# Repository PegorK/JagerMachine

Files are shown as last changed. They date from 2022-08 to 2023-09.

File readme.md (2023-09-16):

# JÄGERMACHINE
<div align="center">
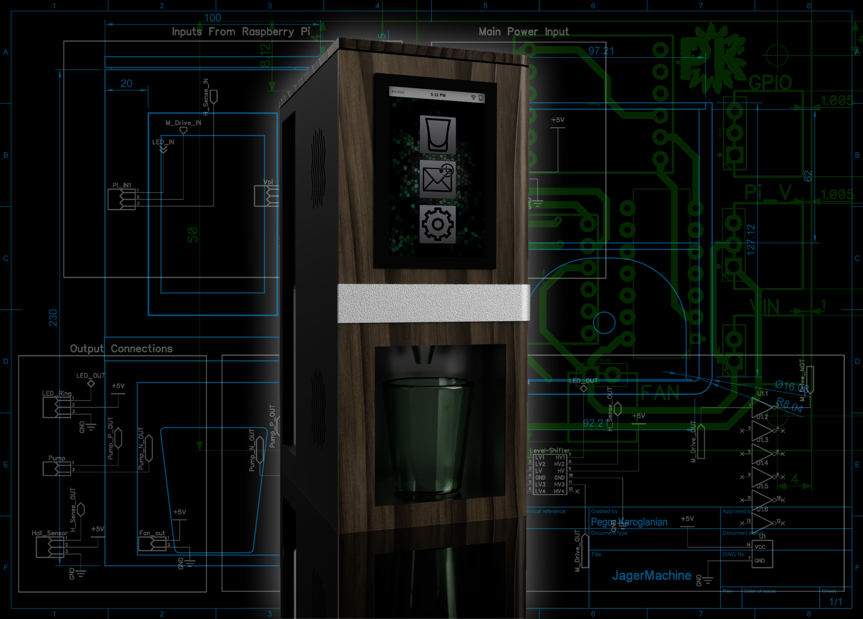
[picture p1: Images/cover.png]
CoverRender
  
</div>

The JägerMachine is an IoT shot pouring machine powered by a Raspberry Pi 3B+. It features a full GUI that allows the user to configure the device, pour a shot, and also check previous messages sent to the machine. Once paired with it's own GMail account, the JägerMachine waits for emails containing a secret user defined subject line and a custom message that gets displayed on the screen. Once an email is received a shot is poured :) 

Initially this project started as a gift for a friend. We always give each other Jagermeister related gifts as an inside joke, so I figured this would be PERFECT. It started out as a pretty bland render I threw together on Fusion 360 as seen below and slowly started getting more and more complicated.

<div align="center">
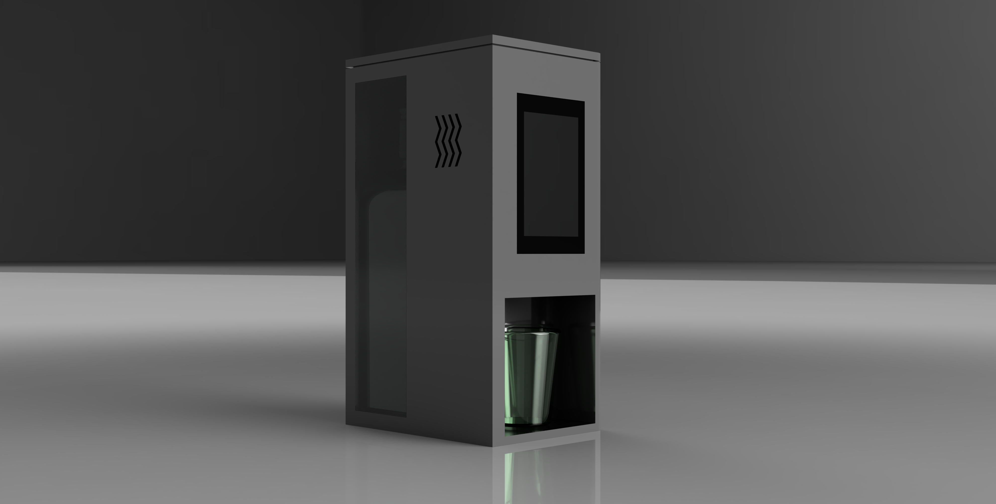
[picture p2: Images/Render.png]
First Render
  
  <br><b>Figure 1</b>: First render of the initial design.
</div>

Unfortunately I didn't finish the project in time for my friends birthday (sorry Jon :( ), but I continued on and kept adding features and I think It's finally done! Some of the features currently supported are as mentioned above are:
* Search for available WiFi connections and connect to them (see Figure 2 & 3).
* Manually pour a shot.
* Pour a shot via email with a a message that gets displayed.
* Hall effect sensor to detect when shot glass is placed/removed.
* Enable/Disable LEDs

<div align="center">
    <table>
        <tr>
            <td>
                <div align="center">
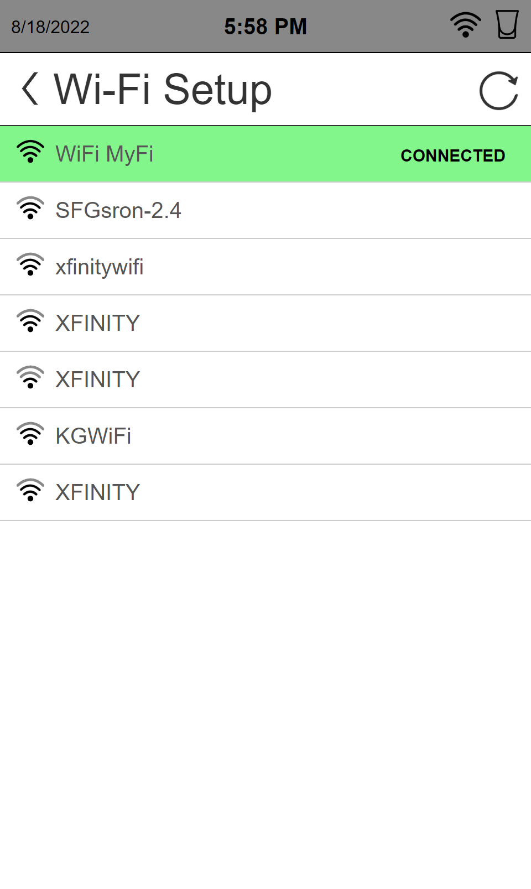
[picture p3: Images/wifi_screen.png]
Wifi Search Screen
                    
                    <br><b>Figure 2.</b>: Available WiFi connections list.
                </div>
            </td>
            <td>
                <div align="center">
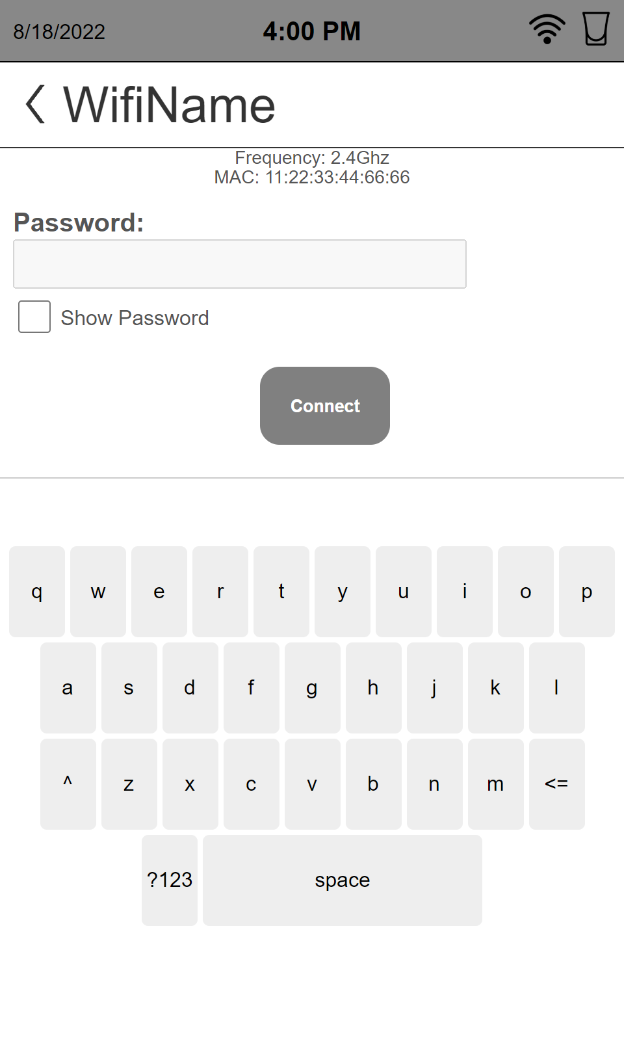
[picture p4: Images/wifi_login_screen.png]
Connect to Wifi
                    
                    <br><b>Figure 3</b>: Signing in to a WiFi connection.
                </div>
            </td>
        </tr>
    </table>
</div>
The hardware for this build wasn't too complicated. I used a logic level shifter to drive the WS2812B LED Ring since it requires 5V logic and RPi outputs 3.3V logic and an H-Bridge Motor driver module for the pump. The only funky part was that I had to use a Hex-Invert IC since the pins I decided to use on the Raspberry Pi are normally high until they are configured as outputs. 

To avoid having a ton of wires everywhere I designed a motherboard PCB that the breakout boards can easily pop onto. The files & schematic for this PCB are in the `Hardware` folder of this repo. The completed board can be seen below. 

<div align="center">
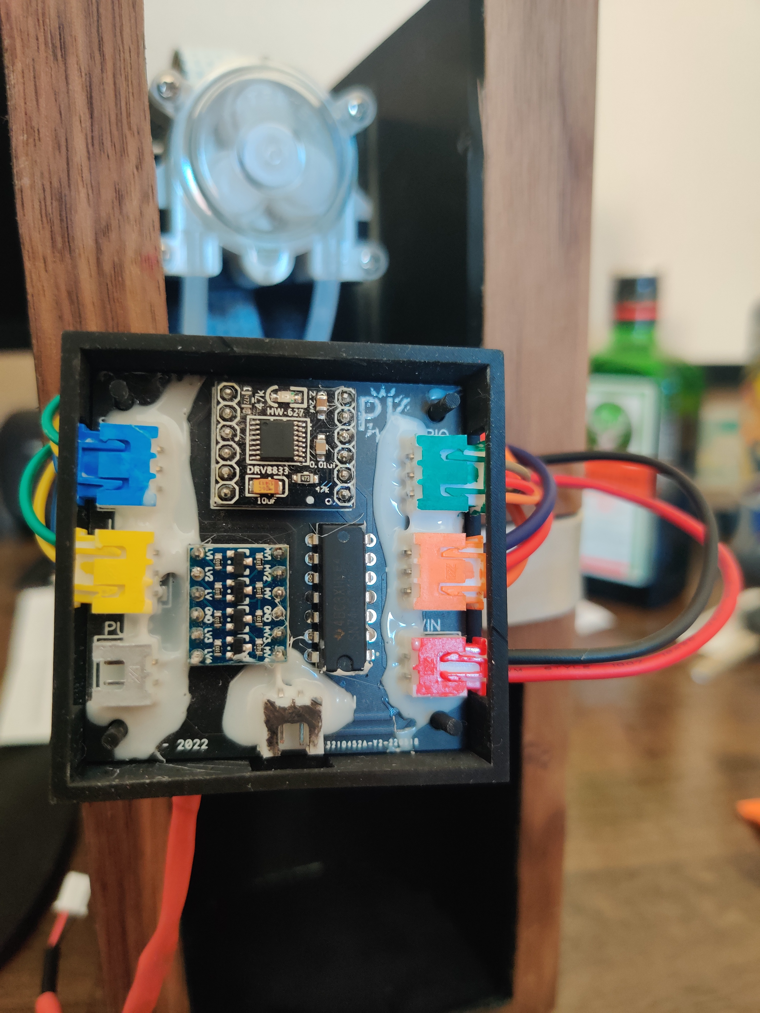
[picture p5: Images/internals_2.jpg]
PCB
    
    <br><b>Figure 4</b>: PCB to connect all peripherals.
</div>

Overall I'd say I got pretty close to the render and vision I originally had in mind. Below are a couple pictures of the JägerMachine booting and pouring a shot.

<div align="center">
    Booting
    <br><b>Figure 5.</b>: JägerMachine booting.
</div>

<div align="center">
    Pouring a shot
    <br><b>Figure 6.</b>: JägerMachine pouring a shot.
</div>

<div align="center">
    Side view
    <br><b>Figure 7.</b>: JägerMachine idle.
</div>

<b>More detailed info on the Raspberry Pi setup can be found below and more pictures are available in the `Images` folder.<b>

<br>

The build parts consist of:
* [3.5" DSI Touch Screen](https://www.amazon.com/dp/B08634Y16L?psc=1&ref=ppx_yo2ov_dt_b_product_details)
* [Peristaltic Pump](https://www.amazon.com/gp/product/B00HLCOXFI/ref=ppx_yo_dt_b_asin_title_o08_s00?ie=UTF8&psc=1)
* [WS2812B LED Ring](https://www.amazon.com/gp/product/B09B3K2XZL/ref=ppx_yo_dt_b_asin_title_o07_s00?ie=UTF8&psc=1)
* [Hall Effect Sensor](https://www.amazon.com/gp/product/B096S7Y2KH/ref=ppx_yo_dt_b_asin_title_o05_s00?ie=UTF8&psc=1)
* [Motor Drive Module (for pump)](https://www.amazon.com/gp/product/B08RMWTDLM/ref=ppx_yo_dt_b_asin_title_o06_s01?ie=UTF8&psc=1)
* [3.3V to 5V Level Shift (for LED ring)](https://www.amazon.com/HiLetgo-Channels-Converter-Bi-Directional-3-3V-5V/dp/B07F7W91LC)
* USB Storage (used to store WiFi info)
* (Optional) Custom PCB (Designed in DipTrace, ordered from PCBWay)
* (Optional) Custom 3D Printed Parts (enclosures, nozzle, pump holder, fan holder)(Designed in Fusion360 ordered from CraftCloud)

## Raspberry Pi Setup Instructions
1)	[Configure Rpi to Kiosk Mode](https://desertbot.io/blog/raspberry-pi-4-touchscreen-kiosk-setup-64-bit-bullseye)
1)	[Install NGINX Webserver (w/ PHP Installation)](https://pimylifeup.com/raspberry-pi-nginx/)
1)	[Enable Root SSH](https://howtovmlinux.com/articles/rasberry-pi/enable-root-login-and-change-password-raspberrypi/)
1)	[Disable BT (optional)](https://di-marco.net/blog/it/2020-04-18-tips-disabling_bluetooth_on_raspberry_pi/)
1)	[Rotate LCD (optional)](https://osoyoo.com/2019/09/20/instruction-for-raspberry-pi-5-dsi-touch-screen/)
1)	[Enable GPIOs](https://pimylifeup.com/raspberry-pi-gpio/)
1)	[Setup NeoPixel libraries](https://learn.adafruit.com/neopixels-on-raspberry-pi/python-usage)
1)	[Setup automount usb flash drive](https://www.shellhacks.com/raspberry-pi-mount-usb-drive-automatically/)
1)	[Add custom splash  (optional)](https://forums.raspberrypi.com/viewtopic.php?t=276545)
1)	[Remove warranty text and other text](https://blog.smittytone.net/2020/05/23/how-to-remove-a-pis-login-message/)
    1) [Hide all boot text](https://techoverflow.net/2021/10/19/how-to-hide-all-boot-text-blinking-cursor-on-raspberry-pi/)
    1) [Hide xorg messages](https://unix.stackexchange.com/questions/110805/debian-squeeze-hide-xorg-start-messages)
1)	[Give root privilege to custom script `runRoot.sh`](https://superuser.com/questions/1448987/allow-php-to-run-shell-script-with-sudo-permission)
1)  Copy over the folders in the `Software` folder (`custom_scripts`, `flags`, `html`, `services`) onto the Raspberry Pi, placing them in `/var/www/`
1)	`Chmod +x` all the scripts under `custom_scripts` folder.
1)	Link the services in the `services` folder to <b>systemd</b>
    1) `boot_complete.service`:
        ```
            systemctl enable /var/www/services/boot_complete.service
        ```
    1) `glass_check.service`:
        ```
            systemctl enable /var/www/services/glass_check.service
        ```
    1) `email_check.service`:
        ```
            systemctl enable /var/www/services/email_check.service
        ```
    1) `wifi_check.service`:
        ```
            systemctl enable /var/www/services/wifi_check.service
        ```
    1) `led_boot.service`:
        ```
            systemctl enable /var/www/services/led_boot.service
        ```
1) Edit the `emailConfig.py` file to your desired email configuration. You must use a GMail account that has two-factor authentication so you can use an app password. [More info on app passwords](https://support.google.com/accounts/answer/185833?hl=en)

### Contact
[Buy me a Coffee!](https://www.buymeacoffee.com/pegor)
<br>
devPegor@gmail.com

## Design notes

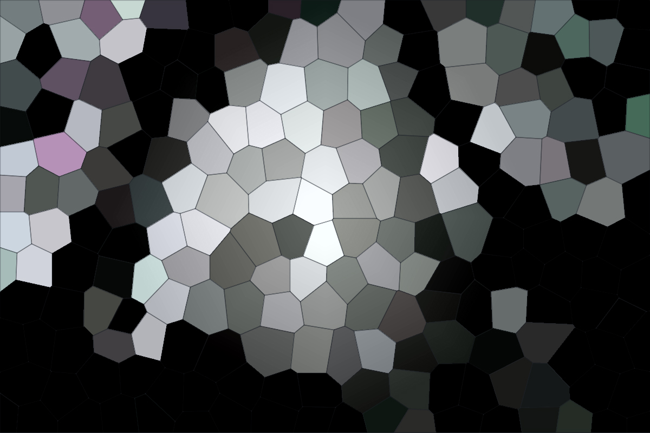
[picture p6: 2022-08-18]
Software/html/images/screen_saver/f_9.jpg

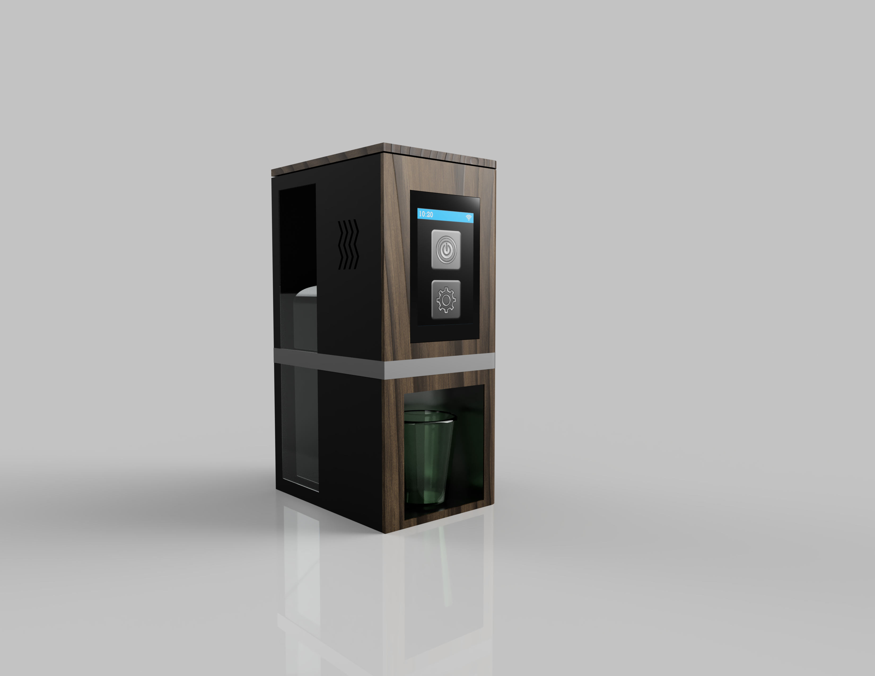
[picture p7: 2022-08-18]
Images/Render_2.png

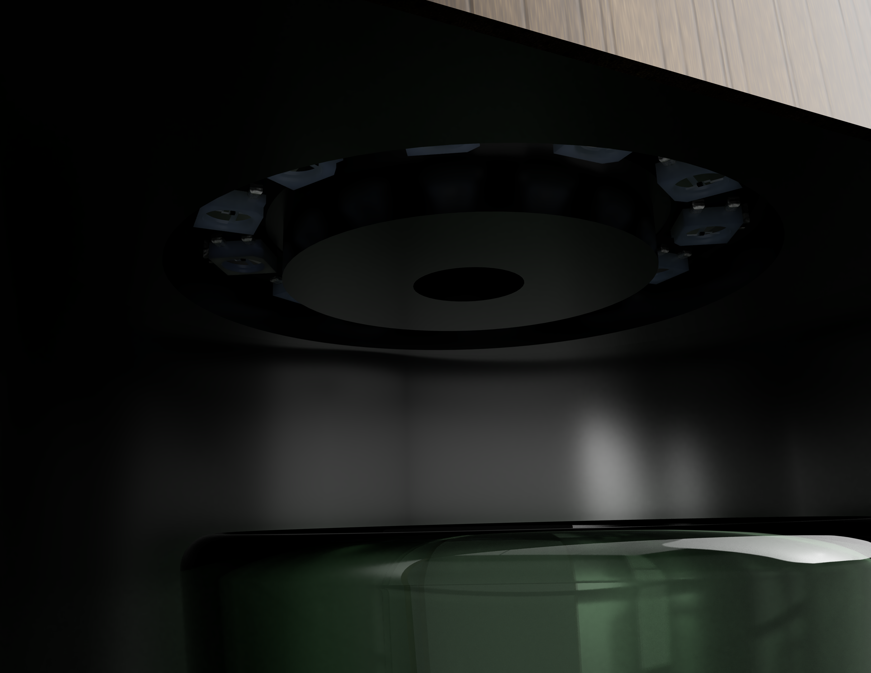
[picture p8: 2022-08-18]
Images/Render_6.png

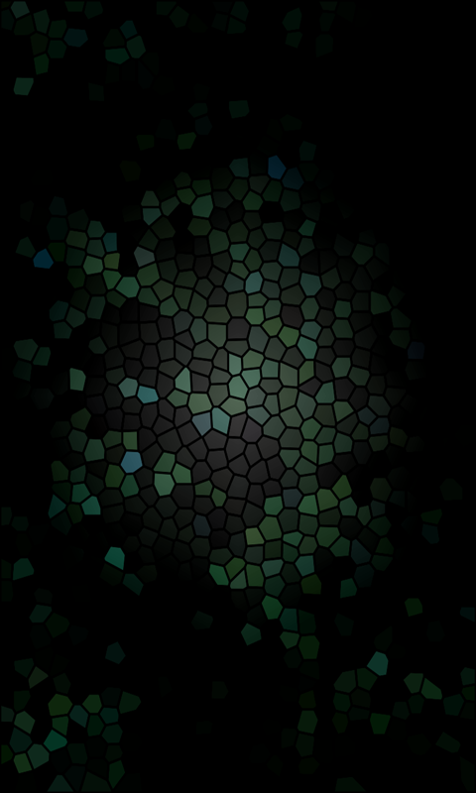
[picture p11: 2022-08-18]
Software/html/images/background_800x480.png

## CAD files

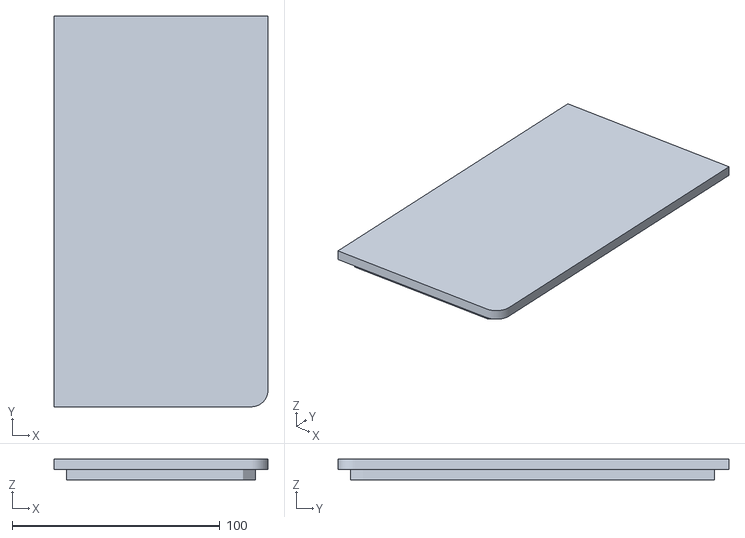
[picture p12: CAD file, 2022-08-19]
Hardware/3D Parts/Main_Lid.stl
103.0 x 188.0 x 10.0

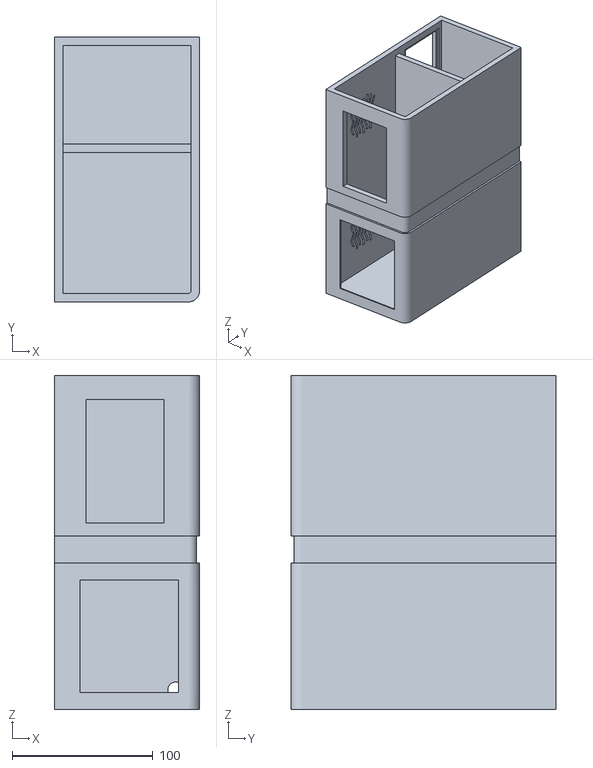
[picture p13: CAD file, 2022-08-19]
Hardware/3D Parts/Main.stl
103.0 x 188.0 x 237.0

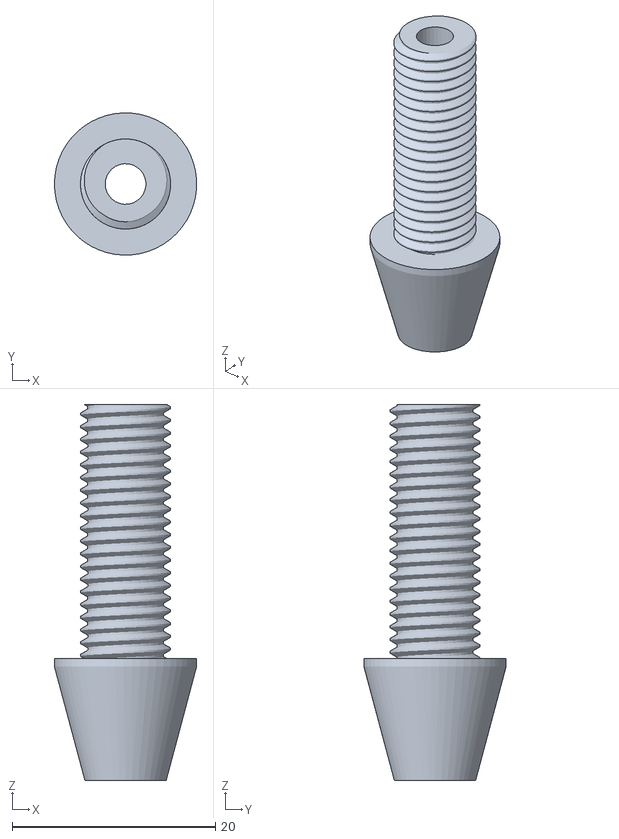
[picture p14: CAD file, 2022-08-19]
Hardware/3D Parts/Nozzle.stl
14.0 x 14.0 x 37.0

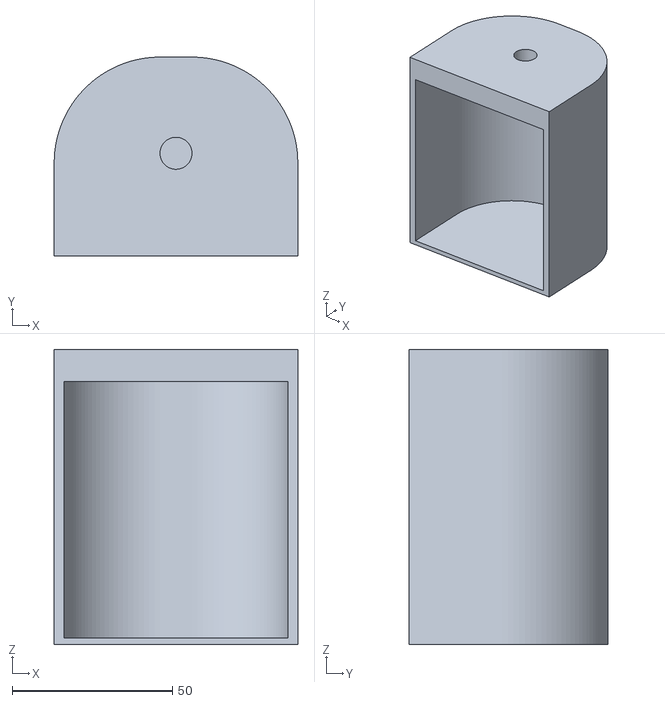
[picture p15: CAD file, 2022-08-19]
Hardware/3D Parts/Shot_Glass_Enclosure.stl
76.0 x 62.0 x 92.0

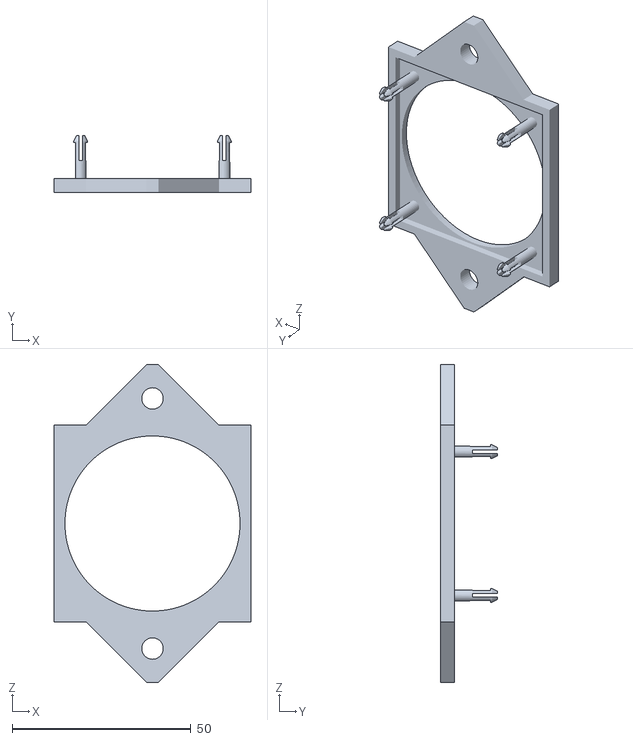
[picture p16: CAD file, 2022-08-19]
Hardware/3D Parts/Fan_Holder.stl
55.0 x 16.0 x 89.0

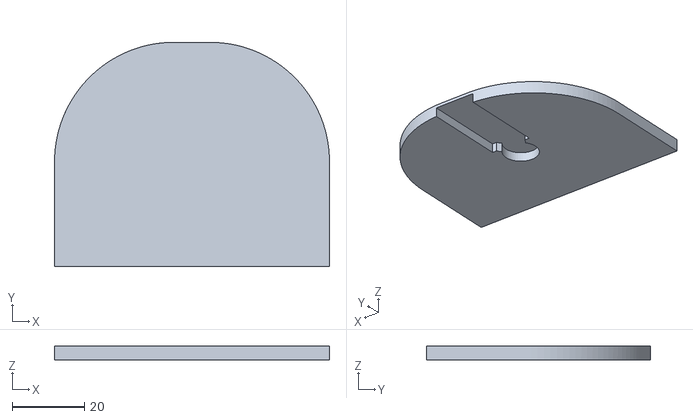
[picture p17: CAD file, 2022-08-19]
Hardware/3D Parts/Hall_Effect_Sensor_Board.stl
76.0 x 62.0 x 4.00

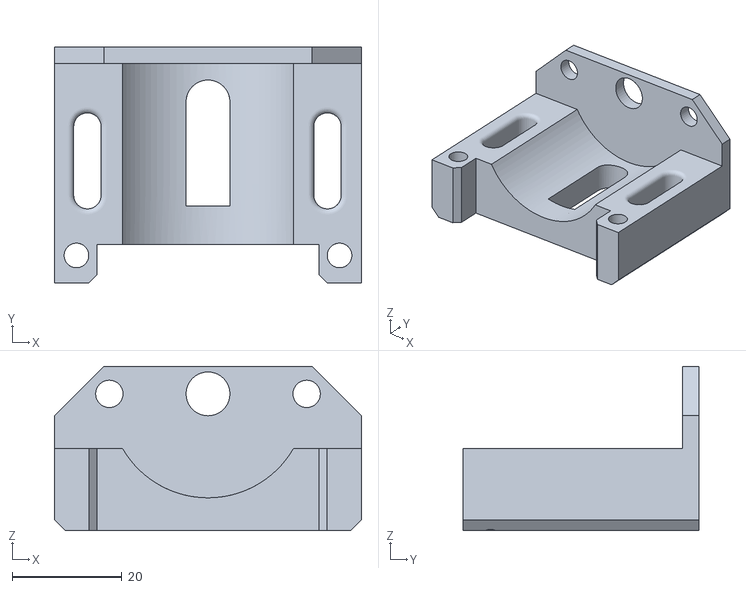
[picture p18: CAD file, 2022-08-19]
Hardware/3D Parts/Pump_Holder.stl
56.0 x 43.0 x 30.0

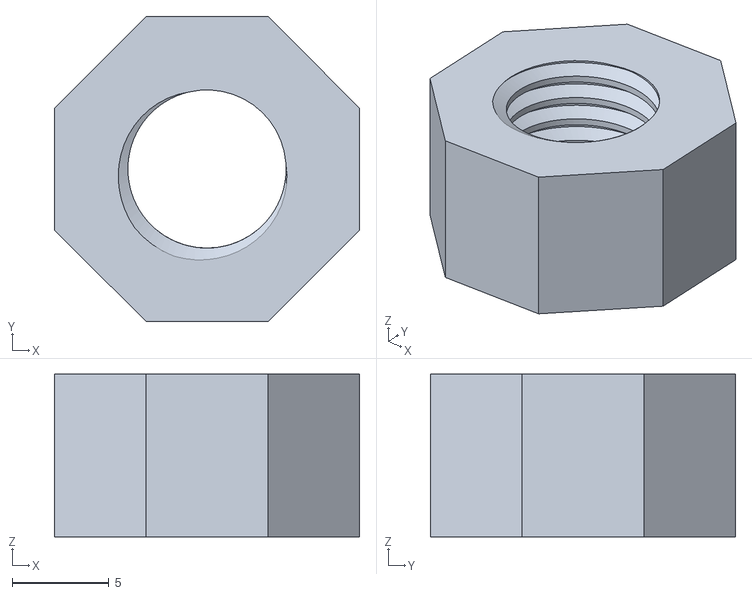
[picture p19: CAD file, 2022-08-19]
Hardware/3D Parts/Nozzle_Nut.stl
15.8 x 15.8 x 8.40

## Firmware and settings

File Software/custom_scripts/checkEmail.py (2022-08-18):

#!/usr/bin/env python

#==========================================
# Title:  checkEmail.py
# Author: Pegor Karoglanian + https://bc-robotics.com/tutorials/sending-email-using-python-raspberry-pi/ (For Emailer class)
# Date:   7/1/22
# Notes:  This script runs continuously and is started by the email-check.service on boot.
#==========================================

import smtplib
import imaplib
import email
import time
import os

import emailConfig as CONFIG

from datetime import datetime, timezone
from urllib.request import urlopen
from pathlib import Path

#Email Variables
SMTP_SERVER         = 'smtp.gmail.com' #Email Server (don't change!)
SMTP_PORT           = 587 #Server Port (don't change!)

GMAIL_USERNAME      = CONFIG.GMAIL_USERNAME
GMAIL_PASSWORD      = CONFIG.GMAIL_PASSWORD
ALLOWED_ADDRESS     = CONFIG.ALLOWED_ADDRESS
SECRET_PHRASE       = CONFIG.SECRET_PHRASE

TIME_THRESHOLD      = 10
RESPONSE_SUBJECT    = "GOT YOUR REQUEST"
RESPONSE_POUR       = "Pouring a shot now :)"
RESPONSE_WAIT       = "Looks like a shot has already been poured and waiting to be cleared. Try again later!"
RESPONSE_NOCUP      = "Look like the shot glass is not in place :( .Try again later!"
RESPONSE_UNK        = "UNKNOWN ERROR >:("

class Emailer:
    def checkNetwork(self):
        try:
            sysWifi = os.popen('sudo /var/www/custom_scripts/runRoot.sh checkOnline')
            return (sysWifi.read().split('\n')[0] == 'True')
        except: 
            return False

    def sendResponse(self, resp):
        #Create Headers
        headers = ["From: " + GMAIL_USERNAME, "Subject: " + RESPONSE_SUBJECT, "To: " + ALLOWED_ADDRESS,
        "MIME-Version: 1.0", "Content-Type: text/html"]
        headers = "\r\n".join(headers)

        #Connect to Gmail Server
        sendSession = smtplib.SMTP(SMTP_SERVER, SMTP_PORT)
        sendSession.ehlo()
        sendSession.starttls()
        sendSession.ehlo()

        #Login to Gmail
        sendSession.login(GMAIL_USERNAME, GMAIL_PASSWORD)

        #Send Email & Exit
        sendSession.sendmail(GMAIL_USERNAME, ALLOWED_ADDRESS, headers + "\r\n\r\n" + resp)
        sendSession.quit

    def checkMail(self):
        readSession = imaplib.IMAP4_SSL('imap.gmail.com')
        readSession.login(GMAIL_USERNAME, GMAIL_PASSWORD)
        readSession.list()

        # Out: list of "folders" aka labels in gmail.
        readSession.select("inbox") # connect to inbox.
        result, data = readSession.uid('search', None, "UNSEEN") # search and return uids instead only for unread email.
        unread_count = len(data[0].split())
        if (unread_count == 0):
            # print("NO UNREAD MESSAGES")
            return False

        latest_email_uid = data[0].split()[-1]
        result, data = readSession.uid('fetch', latest_email_uid, '(RFC822)')

        raw_email = data[0][1]
        email_raw_message = email.message_from_bytes(raw_email)
        email_time = datetime.strptime(email_raw_message['Date'], "%a, %d %b %Y %H:%M:%S %z")
        right_now = datetime.now(timezone.utc)
        time_difference = right_now - email_time

        if ((time_difference.seconds/60) > TIME_THRESHOLD):
            # print("ERROR: Email is old!")
            return False
        
        from_address = email.utils.parseaddr(email_raw_message['From'])[1]

        if (from_address != ALLOWED_ADDRESS):
            # print("ERROR: Received email from invalid sender!")
            return False

        email_subject = email.utils.parseaddr(email_raw_message['Subject'])[1]

        if (email_subject != SECRET_PHRASE):
            # print("ERROR: Email doesn't have right secret phrase!")
            return False

        email_content = email_raw_message.get_payload(0).get_payload().split('\r\n')
        return(email_content[0])

#####################################################################################################################


emailChecker = Emailer()
delayBetweenChecks = 30  # seconds

while True:
    try:
        if (emailChecker.checkNetwork()):
            delayBetweenChecks = 30  # seconds
            newEmail = emailChecker.checkMail()
            respone = ""
            if (newEmail == False):
                print(False)
            else:
                shotFlag = '/var/www/flags/shot.flag'
                shotRemovedFlag = '/var/www/flags/shot_removed.flag'
                msgFile  = '/var/www/flags/msg.txt'
                glassFlag = '/var/www/flags/glass.flag'

                # Check whether the shot flag exists or not
                # this flag gets cleared when the displayed message is cleared.
                shotCheck = os.path.exists(shotFlag)

                #this flag gets cleared when the shot glass is taken out of the tray.
                shotCheck_2 = os.path.exists(shotRemovedFlag)

                # Check whether the shot glass is present
                glassCheck = os.path.exists(glassFlag)

                if not glassCheck:
                    emailChecker.sendResponse(RESPONSE_NOCUP)
                    print(False)
                elif not shotCheck and not shotCheck_2:
                    # Looks like a shot hasn't been poured yet so go ahead and pour and set the two flags
                    # and write the message to a file to be read by webui.
                    os.popen('sudo /var/www/custom_scripts/runRoot.sh pourShot &')

                    text_file = open(msgFile, "w")
                    newMsg = text_file.write(newEmail)
                    text_file.close()

                    Path(shotFlag).touch()

                    emailChecker.sendResponse(RESPONSE_POUR)
                    # start pouring shot!
                    # print("POURING A SHOT!")
                    print(newEmail)
                else:
                    emailChecker.sendResponse(RESPONSE_WAIT)
                    # print("Looks like a shot has already been poured. Waiting to clear the flag.")
        else:
            print("No network detected. Increasing delay before checking again.")
            delayBetweenChecks = 60 # seconds
    except OSError as err:
        print("OS error: {0}".format(err))
    except BaseException as err:
        print(f"Unexpected {err=}, {type(err)=}")

    time.sleep(delayBetweenChecks)

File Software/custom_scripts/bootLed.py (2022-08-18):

#!/usr/bin/env python3

#==========================================
# Title:  bootLed.py
# Author: Pegor Karoglanian
# Date:   7/1/22
# Notes:  This script starts up the boot LED sequence until boot is complete.
#==========================================


import sys
import board
import neopixel
import time
import os 
import random

LEDs = 12
ledRing = neopixel.NeoPixel(board.D18, LEDs)

ledTail_1 = 0
ledTail_2 = 0
ledOff = 0

bootComplete = os.popen('systemctl is-system-running')
bootComplete = bootComplete.read().strip()
if bootComplete == "degraded" or bootComplete == "running":
    for y in range(10):
        for x in range(LEDs):
            r_r = random.randint(0, 200)
            r_g = random.randint(0, 200)
            r_b = random.randint(0, 200)
            ledRing[x]    = (r_r, r_g, r_b)
            time.sleep(0.01)

    for y in range(20):
        for x in range(LEDs):
            ledRing[x]    = (0, 255-(y*13), 0)
        time.sleep(0.03)
    for x in range(LEDs):
        ledRing[x] = (0, 0, 0) 
else:
    while True:
        for x in range(LEDs):
            ledRing[ledOff]    = (0, 0, 0)
            ledRing[ledTail_2] = (0, 102, 0)
            ledRing[ledTail_1] = (0, 153, 0)
            ledRing[x]         = (0, 204, 0)

            ledTail_1 = x
            ledTail_2 = x - 1
            if (ledTail_1 == -1):
                ledTail_1 = 11

            ledOff = x - 2
            if (ledTail_2 == -1):
                ledTail_2 = 11
            elif (ledTail_2 == -2):
                ledTail_2 = 10
            time.sleep(0.06)
